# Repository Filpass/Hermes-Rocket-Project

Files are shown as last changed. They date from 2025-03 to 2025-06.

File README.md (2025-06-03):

# Hermes Rocket Project 🚀

This repository contains all software, data, and design files used in the development and flight testing of the Hermes Rocket.

## 📂 Contents

- `Design_Fabrication_and_Testing_of_a_3D_Printed_Model_Rocket_with_Integrated_Telemetry_Systems.pdf` – Master's thesis submitted for the M.Sc. in Space Engineering at Universität Bremen
- `/cad` – 3D models of nose cone, body tube, and adapter (.STL)
- `/code` – Python scripts for telemetry collection, live plotting, and post-flight analysis
- `/data` – Raw telemetry data from each flight (CSV format)
- `/analysis` – Static plots generated from telemetry

📄 [Download the full thesis (PDF)](./Design_Fabrication_and_Testing_of_a_3D_Printed_Model_Rocket_with_Integrated_Telemetry_Systems.pdf)

## 🛰️ Hardware Overview

- **Main Computer:** Raspberry Pi Zero 2W  
- **Sensors:**
  - GPS Module: PA1010D  
  - Barometric Pressure Sensor: DPS310  
  - 9-DOF IMU: ICM-20948 

## 📈 Output

Post-flight data visualization is located in the `/analysis` folder.

## 📹 Videos

Due to GitHub storage limits, flight camera and telemetry videos are hosted externally:  
🎥 [Watch on YouTube (Unlisted)](https://www.youtube.com/playlist?list=PLU9vdCkJsIVlVfhIgIDVsfnCWYGNboWbm)

## 📜 License

This project is open-source under the [MIT License](./LICENSE).

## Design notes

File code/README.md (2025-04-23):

# Hermes Rocket Project 🚀

This file contains all the python files that were used the project, in order to create this files the help of ChatGPT was used.

## Contents

- `camery.py` - Is the script for the camera to start recording
- `post_flight_plot.py` - Is the script in order to re watch the telemetry after the flight
- `receive_live2.py` - Is the script for the ground station in this case the macbook I had 
- `send_data3.py` - Is the script for the raspberry pi, specifically for the sensors to work. It needs to be run separately from the camera.py script as most of the libraries can only be used in a virtual environment
- `video_merge.py` - Is the script that merges all the video files and then converts them from .h264 to mp4 
- `flight_simulation.py` - Is the script that simulates the movement of the rocket based on its accelerometer and gyroscope data.

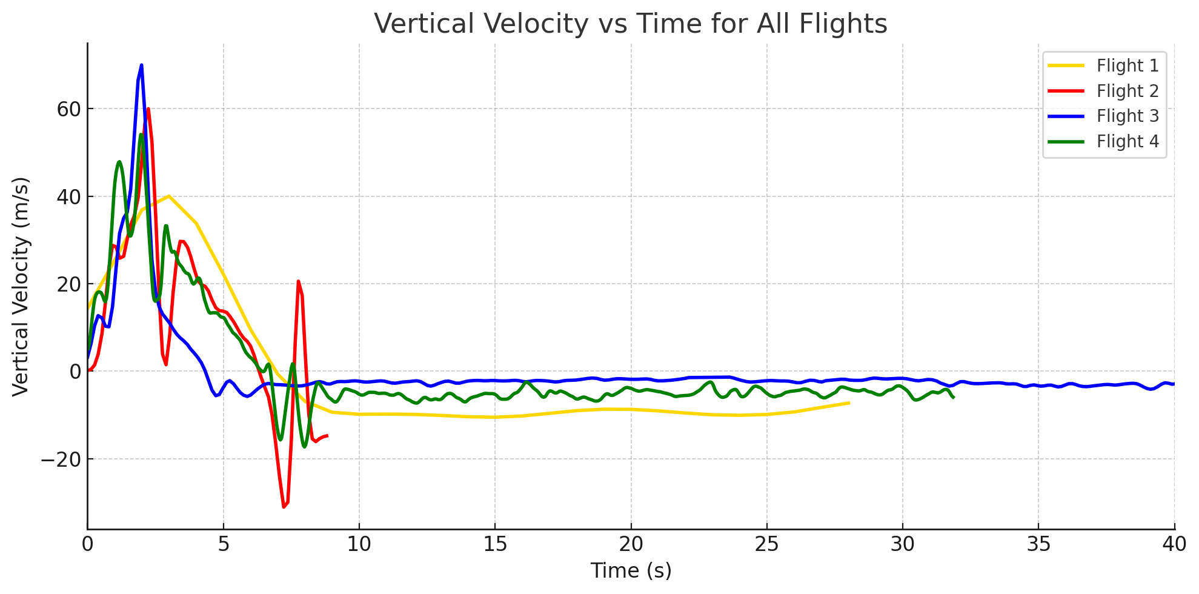
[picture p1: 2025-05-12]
analysis/Vertical Velocity vs Time for All Flights.png

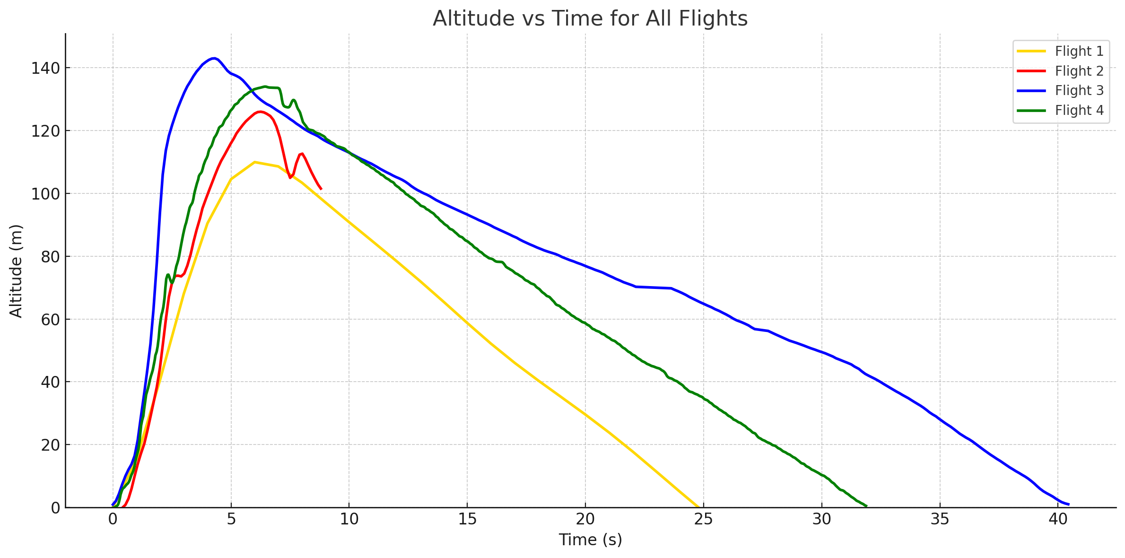
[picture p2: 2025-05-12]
analysis/Altitude vs Time for All Flights.png

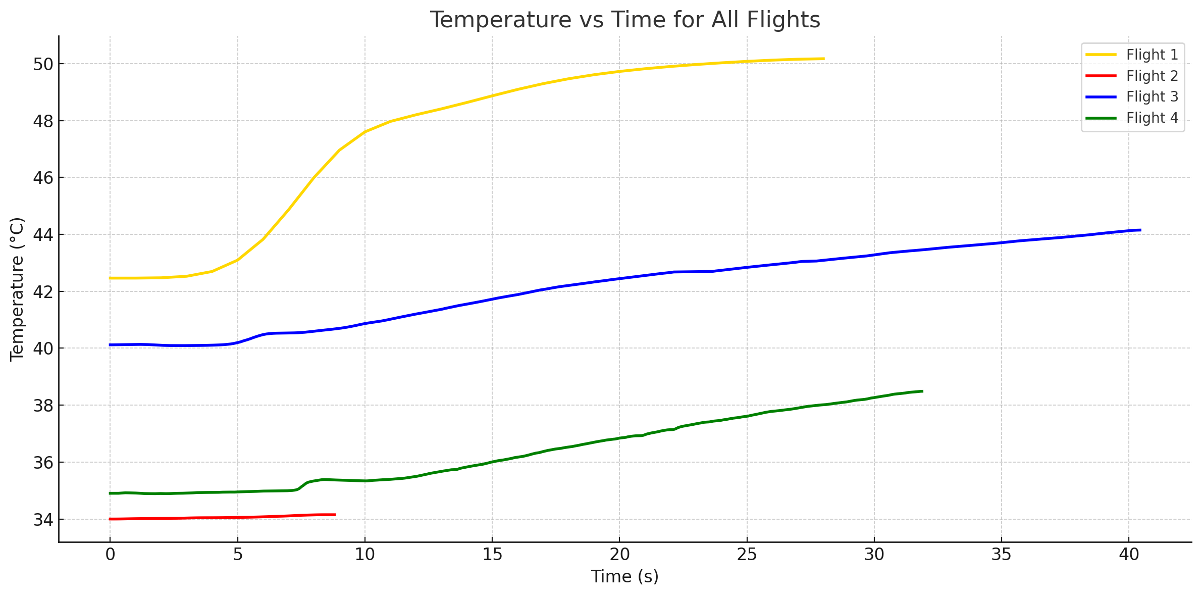
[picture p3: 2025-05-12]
analysis/Temperature vs Time for All Flights.png

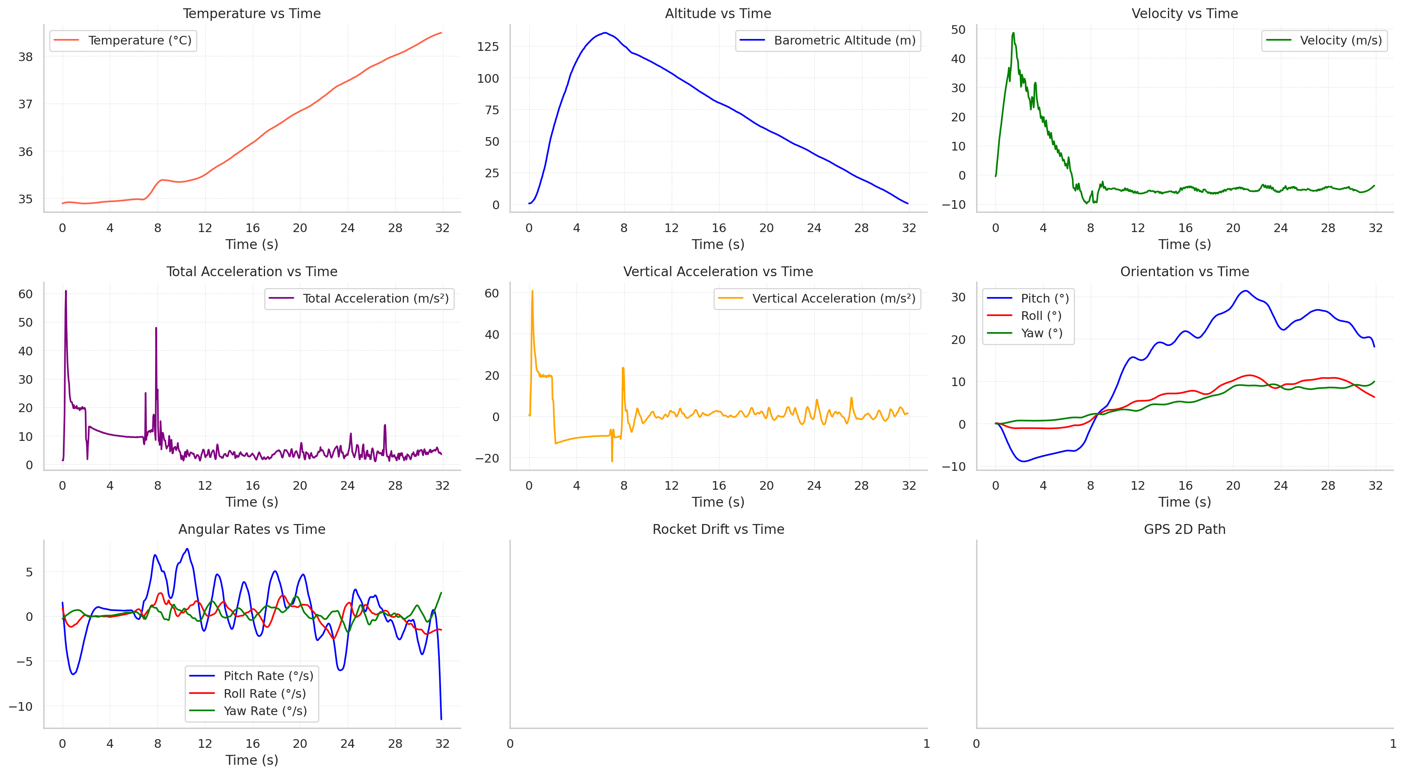
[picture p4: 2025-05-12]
analysis/Flight 4 - Telemetry.png

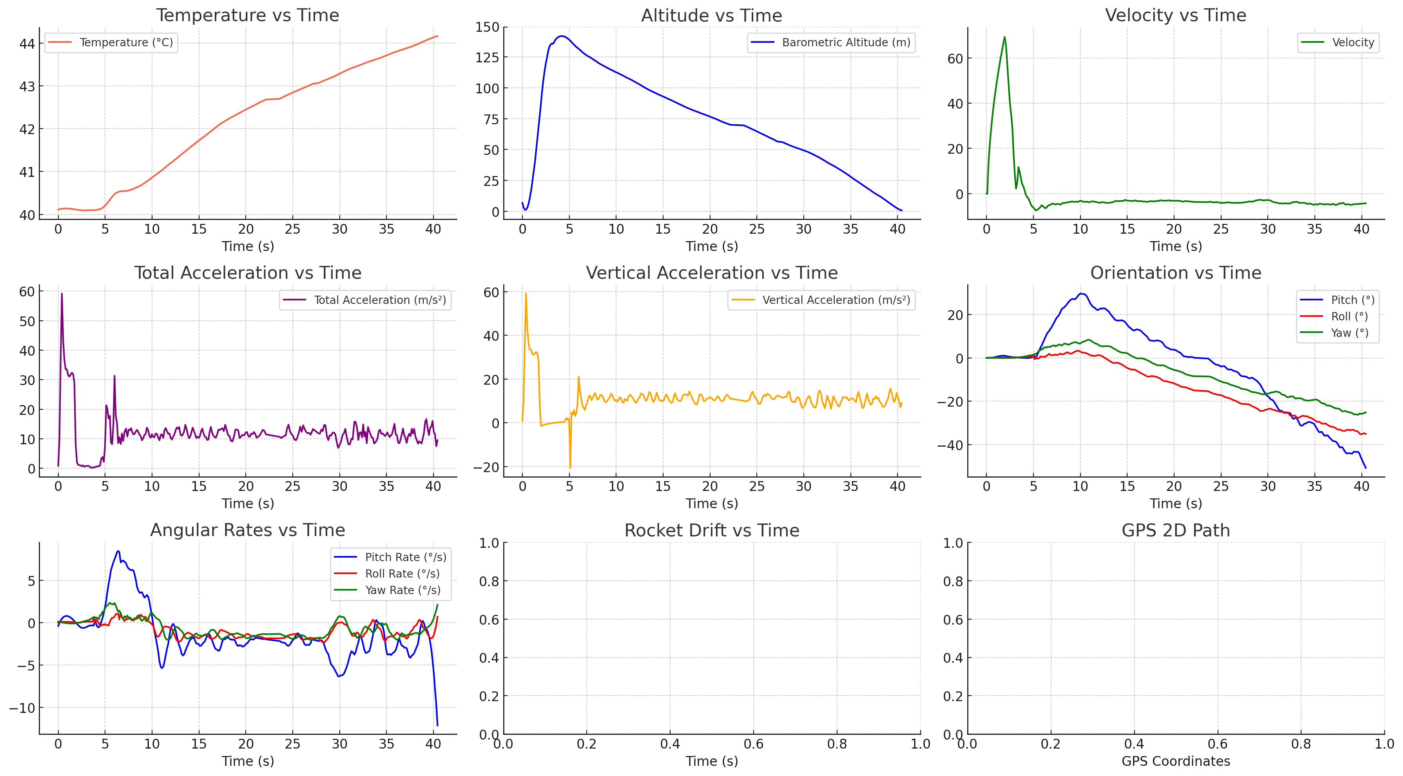
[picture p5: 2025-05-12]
analysis/Flight 3 - Telemetry.jpeg

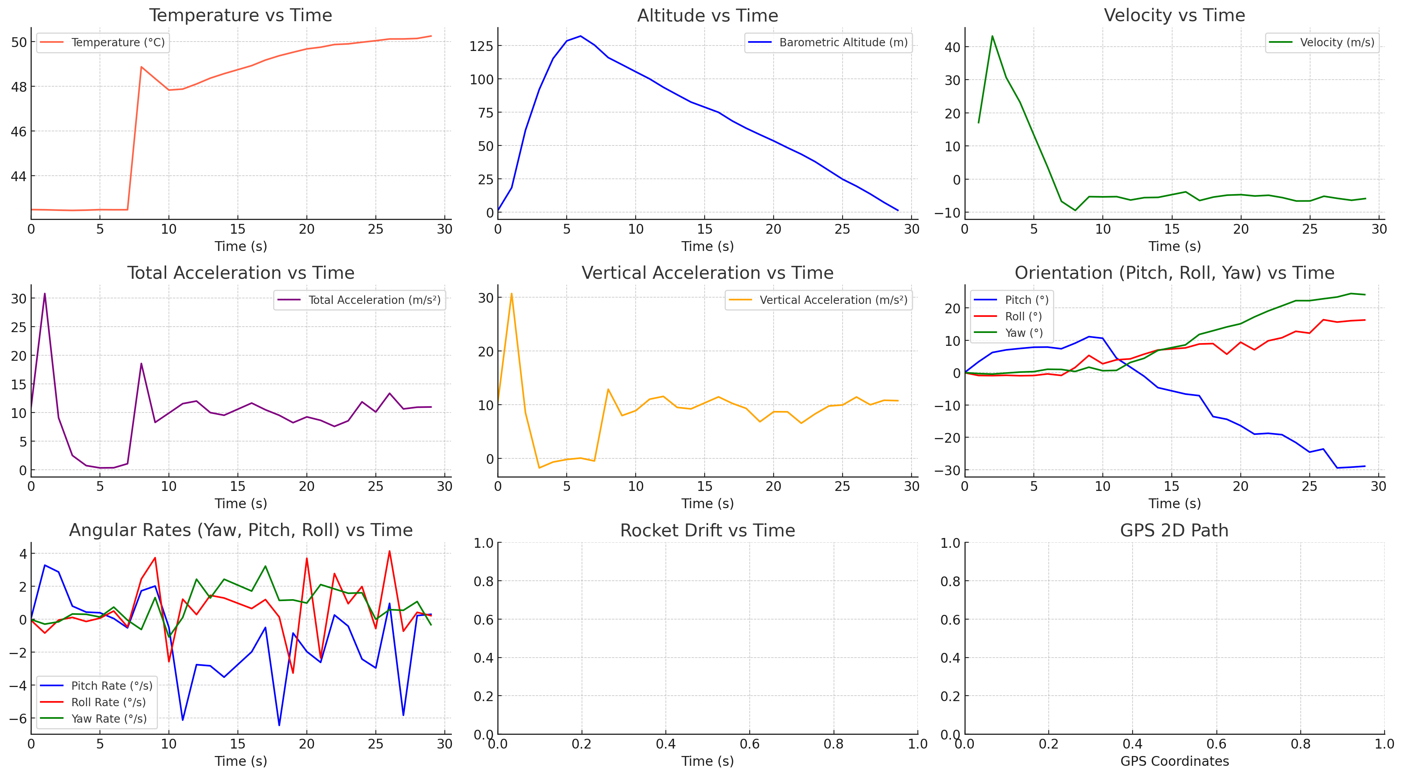
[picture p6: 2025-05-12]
analysis/Fligth 1 - Telemetry.png

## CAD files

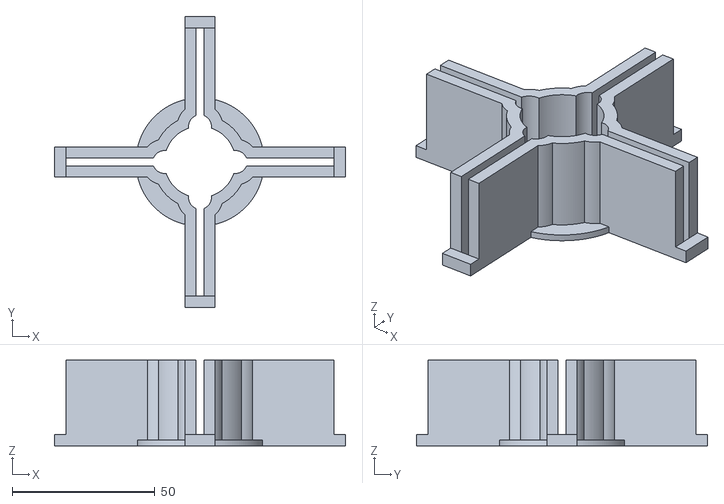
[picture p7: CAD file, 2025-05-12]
cad/Hermes Fin Aligner.stl
102.0 x 102.0 x 30.0

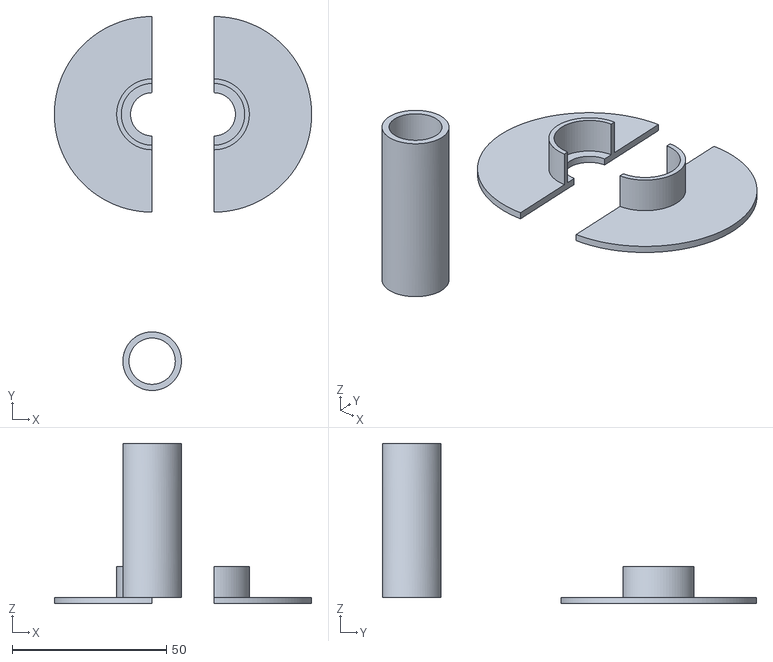
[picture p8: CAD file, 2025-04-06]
cad/Hermes Engine Protection.stl
83.4 x 121.2 x 52.0

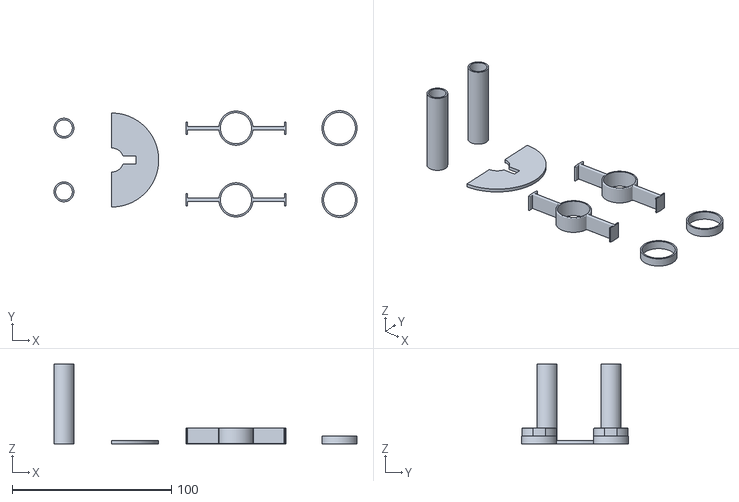
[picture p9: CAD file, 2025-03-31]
cad/Hermes Tubes.stl
190.2 x 67.0 x 50.0

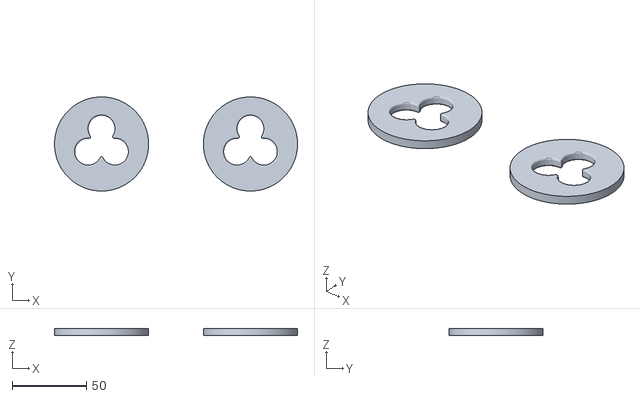
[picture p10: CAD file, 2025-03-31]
cad/Hemres BT Engine Mount.stl
163.2 x 63.2 x 5.00

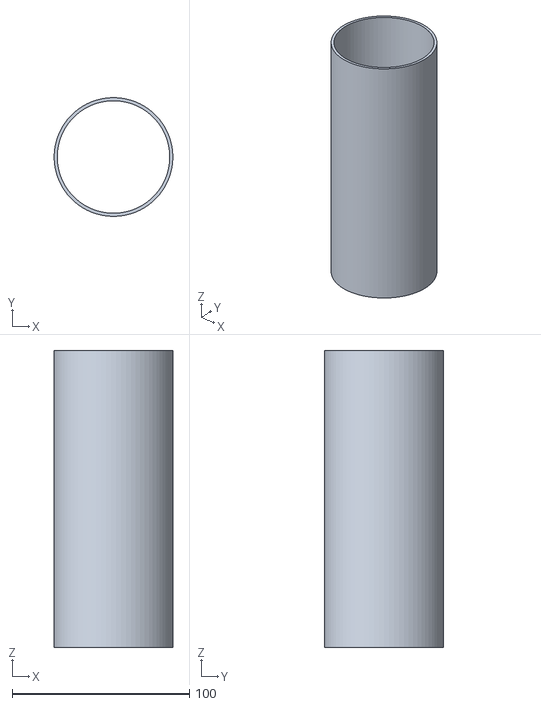
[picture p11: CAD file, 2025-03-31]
cad/Hermes BT.stl
67.0 x 66.9 x 167.5

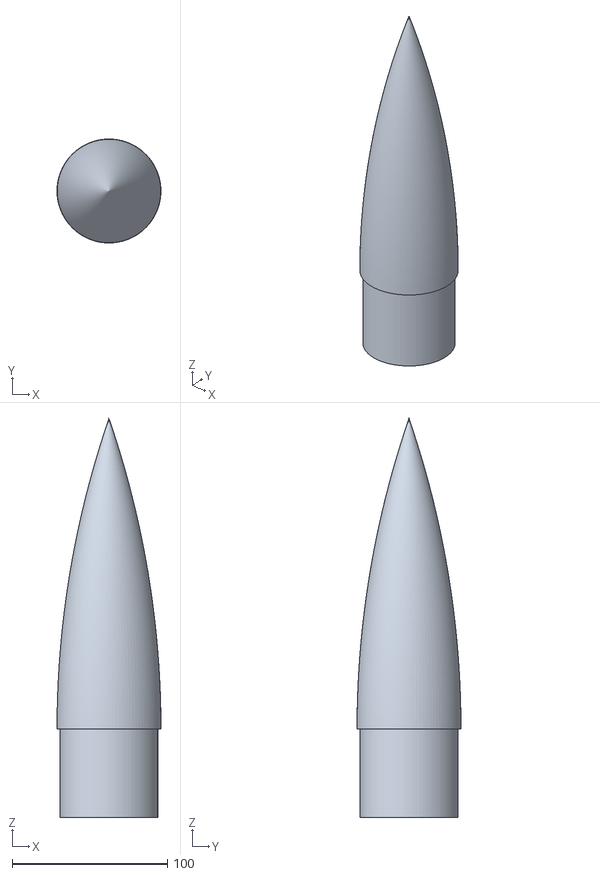
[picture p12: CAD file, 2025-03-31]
cad/Hermes NC.obj
67.0 x 67.0 x 257.0

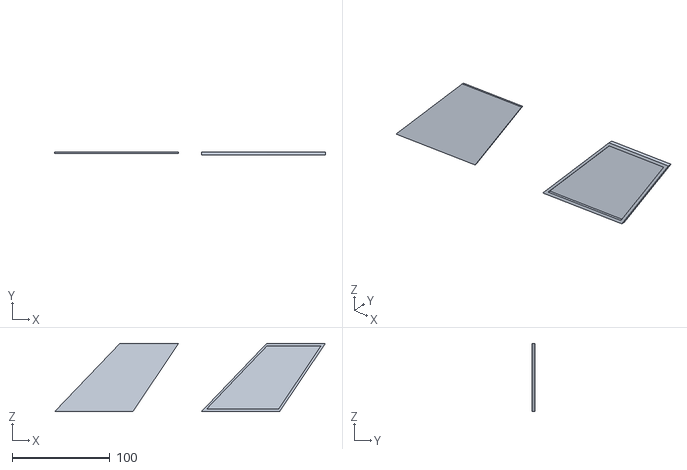
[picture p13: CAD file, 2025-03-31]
cad/Hermes Fin.stl
277.0 x 3.50 x 70.0

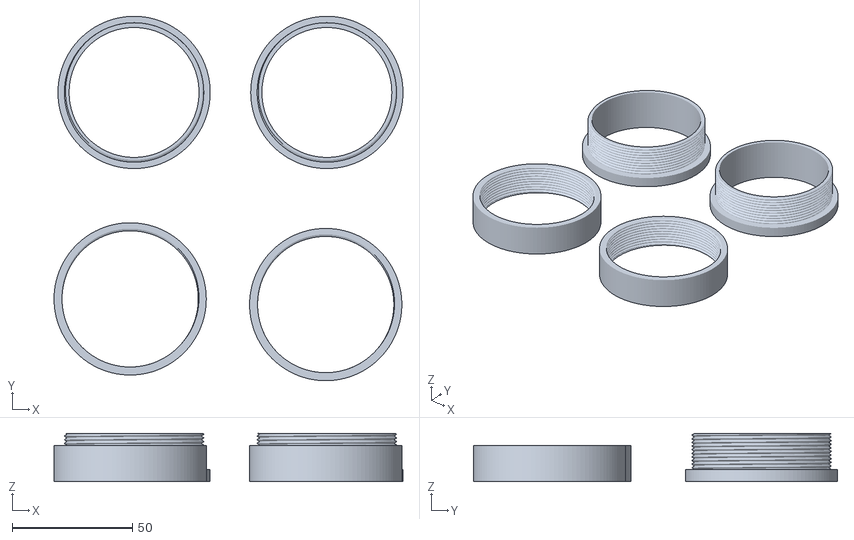
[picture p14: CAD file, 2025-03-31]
cad/Hermes BT Screwed Adapter.stl
144.8 x 151.2 x 20.0

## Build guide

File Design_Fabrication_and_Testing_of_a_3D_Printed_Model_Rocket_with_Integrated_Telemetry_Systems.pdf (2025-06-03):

## University of Bremen

## Faculty 4 Production Engineering

## Master Space Engineering I

## Master Thesis

# Design, Fabrication, and Testing of a 3D-Printed Model Rocket with Integrated Telemetry Systems

Author: | Philippos Georgios Moschidis Mat. Nr. 6254474
Date: | 06.06.2025
1. Reviewer: Dr.-Ing. Benny Rievers
2. Reviewer: Dr.-Ing. Florian Meyer

Supervisor: Dr. Petros Bithas

Philippos Georgios Moschidis Master Thesis
moschidis.filip@gmail.com
Matriculation Nr. 6254474

Design, Fabrication, and Testing of a 3D-Printed Model Rocket with Integrated Telemetry Systems

Entwurf, Herstellung und Test einer 3D-gedruckten Modellrakete mit integrierten Telemetriesystemen

Reviewers: Prof. Dr.-Ing. Benny Rievers & Dr. Florian Meyer Supervisors: Dr. Petros Bithas
University of Bremen
Space Engineering I (SpE I)
Faculty 4 Production Engineering ZARM, Am Fallturm 2
28359 Bremen

ii

## Abstract

The Hermes Rocket Project focuses on the integration of modern technologies into model rocketry through the design and fabrication of a 3D-printed rocket that includes a telemetry system. The objective of this study is to develop a costeffective and reusable model rocket capable of achieving an apogee of over 150 meters. The rocket is designed to collect flight data while it also utilises a camera to analyse the flight trajectory post-flight. The rocket has been designed to be lightweight and stable, while also ensuring structural integrity, based on PETG material and modular 3D-printed components. The flight computer, which has been custom-built, includes a Raspberry Pi Zero 2W microcontroller at its core, as well as three sensors: a GPS, an inertial measurement unit (IMU), and a barometric sensor to monitor altitude, pressure, and motion data. With these sensors we can monitor data which can be observed live during the start of the launch and more important they will be analysed post launch together with the onboard video footage. The propulsion of the rocket is provided by Klima D9-5 rocket engines, while the design, simulation and stability of the rocket were ensured through the use of OpenRocket software. The recovery system consists of a ripstop nylon parachute. There were four test flights completed that validated the rocket’s performance, telemetry accuracy, and recovery system. The flight data that were collected showed an okay alignment with OpenRocket simulations, with some deviations primarily because of environmental conditions and possibly motor performance. The results confirm the feasibility of using low-cost 3D-printed systems and off-the-shelf components for educational and experimental aerospace applications. This research shows how 3D printing and modern sensors can make model rockets easier to use and perform better, providing valuable information for educational and amateur aerospace projects.

iii

## Contents

1. Introduction | 2
2. Literature Review | 5
2.3. Role of Flight Computers and Telemetry in Model Rockets . . . . | 10
3. Rocket Design and Fabrication | 11
3.2.1. PLA, PETG, ABS, and Carbon Fiber Nylon Properties . . | 12
4. Flight Computer and Sensor Integration | 22
4.4.2. Data Logging, Visualization, and Ground Station Integration 30

iv

5. Propulsion System | 33
6. Rocket Simulation and Stability Analysis | 35
6.1.1. Centre of Gravity (CG) and Centre of Pressure (CP) . . . | 35
6.3. OpenRocket Documentation and Justification of Simulation
6.3.4. OpenRocket Simulation Features and Output Parameters . | 41
7. Recovery System Design | 43
8. Testing and Validation | 45
9. Results and Discussion | 48
10.Conclusion and Future Work | 72

v

10.4. Potential Applications of the Hermes Rocket | | 74
References | i
A. Project Repository | iii
B. Component List and Costs | iii
C. Launch Day Checklist | iii
D. Declaration of Consent | iv

vi

## List of Figures

1. Shady Side Academy Rocketry Club, Pittsburgh PA in January
| 1965. Rocketry enthusiasts from over a half century ago [2]. . . . | 2
2. | Hermes Rocket before the first Flight | | 3
3. | Four Forces in Flight [3] | | 5
4. Relativity Space’s third generation 3D-printer in its new head-
| quarters, with CEO Tim Ellis standing by for scale [9] | | 9
5. | Hermes Rocket with labeled parts | | 11
6. PLA, PETG, and ABS are the most common materials used with
| filament 3D Printers [12] | | 13
7. | Body Tube of Hermes on Fusion 360 | | 15
8. | Nose cone and Shoulder of Hermes on Fusion 360 | | 16
9. | Fins of Hermes on Fusion 360 | | 18
10. Hollow Interior Fin Design | | 18
11. The Original Prusa MINI+ Printer | | 19
12. The screwed adapter on Fusion360 and printed | | 20
13. The threaded adapter on Fusion360 | | 21
14. Flight Computer | | 22
15. Raspberry Pi Zero 2W and SparkFun Qwiic/STEMMA QT HAT
| [14] | | 23
16. Adafruit TDK InvenSense ICM-20948 [14] | | 25
17. Adafruit Mini GPS PA1010D [14] | | 25
18. Raspberry Pi Camera Module 3 - 12MP 120 Degree Wide Angle
| Lens [14] | | 26
19. LP903450 3.7 V 800 mAh Lithium Polymer Battery | | 27
20. The tube with the Raspberry Pi and sensors | | 28
21. Camera and GPS | | 29
22. Data Visualisation | | 32
23. Klima D9-5 engines | | 33
24. Thrust Curve of Klima D9-5 Engine [15] | | 34
25. Engine Mount on Fusion 360 | | 34
26. The three stability conditions with their CG-CP | | 36
27. Weight Distribution | | 37
28. A diagram of the rocket component classes [5] | | 38
29. The parachute system with dimensions | | 44
30. On-Board photo from Flight 1 | | 49
31. Telemetry data from the first flight | | 50
32. Flight 1 - Comparison of Actual and Simulated Altitude | | 51
33. Flight 1 - Comparison of Actual and Simulated Velocity | | 51
34. Flight 1 - Comparison of Actual and Simulated Total and Vertical
| Accelerations | | 52
35. Ejection Charge Protection System | | 53

vii

36. Telemetry data from the second flight | | 54
37. Flight 2 - Comparison of Actual and Simulated Altitude | | 55
38. Flight 2 - Comparison of Actual and Simulated Velocity | | 56
39. Flight 2 - Comparison of Actual and Simulated Total Acceleration | 56
40. Flight 2 - Comparison of Actual and Simulated Vertical Acceleration 57
41. Telemetry data from the third flight | | 58
42. On-Board photo from Flight 3 | | 59
43. Flight 3 - Comparison of Actual and Simulated Altitude | | 60
44. Flight 3 - Comparison of Actual and Simulated Velocity | | 60
45. Flight 3 - Comparison of Actual and Simulated Total Acceleration | 61
46. Flight 3 - Comparison of Actual and Simulated Vertical Acceleration 61
47. On-Board photo from Flight 4 | | 62
48. Telemetry data from the fourth flight | | 63
49. Flight 4 - Comparison of Actual and Simulated Altitude | | 64
50. Flight 4 - Comparison of Actual and Simulated Velocity | | 64
51. Flight 4 - Comparison of Actual and Simulated Total Acceleration | 65
52. Flight 4 - Comparison of Actual and Simulated Vertical Acceleration 65
53. Temperature Comparison of All Flights | | 66
54. Altitude Comparison of All Flights | | 66
55. Vertical Velocity Comparison of All Flights | | 67
56. Actual vs Simulated Flight Durations | | 68
57. Total Acceleration Comparison of All Flights | | 68
58. Controllable Surfaces on Fins by BPS.space [19] | | 74

viii

## List of Tables

1. | Comparison of 3D Printing Materials | | 12
2. | Comparison of Barometric Pressure Sensors [14] | | 24
3. Summary of key simulation assumptions in OpenRocket and their
| potential impacts on accuracy | | 42
4. | Requirement Description and Verification Method | | 45
5. | Flight Conditions and Environment Summary | | 48

ix

## List of Abbreviations

ABS | Acrylonitrile Butadiene Styrene
BMP | Barometric Pressure Sensor
CAD | Computer-Aided Design
Cal | Caliber (distance between CG and CP in body diameters)
CD | Drag Coefficient
CG | Centre of Gravity
CP | Centre of Pressure
DC | Direct Current
DOF | Degrees of Freedom
DPS310 | Digital Pressure Sensor 310
FDM | Fused Deposition Modeling
FPS | Frames Per Second
GND | Ground (electrical)
GPIO | General-Purpose Input/Output
GPS | Global Positioning System
HAT | Hardware Attached on Top
Hz | Hertz (sampling rate)
I2C | Inter-Integrated Circuit
IC | Integrated Circuit
IMU | Inertial Measurement Unit
J-B Weld | Commercial Two-Part Epoxy Adhesive
LED | Light Emitting Diode
mAh | Milliamp Hours
M58x1.5 | ISO Metric Thread (58 mm diameter, 1.5 mm pitch)
NAR | National Association of Rocketry
NASA | National Aeronautics and Space Administration
PETG | Polyethylene Terephthalate Glycol
PLA | Polylactic Acid
RAM | Random Access Memory
SBC | Single-Board Computer
SPI | Serial Peripheral Interface
STEM | Science, Technology, Engineering and Mathematics
STEMMA QT Adafruit Quick Connect I2C System
UDP | User-Datagram Protocol
V Voltage
°C | Degrees Celsius
°/s | Degrees per second
µA | Microamperes
µT | Microtesla

x

## Acknowledgement

I would like to thank several people whose support and guidance were crucial to completing my thesis. My academic supervisors, Dr. Benny Rievers and Dr. Florian Meyer, provided continuous guidance and constructive feedback throughout this process, and their support was very valuable. Their expertise was crucial to the completion of this thesis.

Additionally, I am especially thankful to my external supervisor, Dr. Petros Bithas, who without hesitation offered to help me with another thesis and whose contribution led to the successful completion of this project.

In particular, I would like to thank Mr. Theodoros Papafotiou for his support, very helpful ideas and for giving me access to the laboratory facilities of ’VROOM’, which were essential for the development of this thesis.

Finally, I wish to thank my family and friends for their support, patience and motivation during this challenging journey.

“Engineering is at the heart of space exploration, turning bold ideas into tangible achievements solving problems that were once considered impossible.”
− Aerospace Engineer

## 1. Introduction

### 1.1. Background and Purpose of the Study

The field of model rocketry started in the United States in 1957, it resulted from a synthesis of model aviation, the ancient art of pyrotechnics and modern rocket technology. It spawned the development of a novel and innovative approach to the field of model rocketry. Rocketry has for a long time been a platform for scientific exploration, offering students and hobbyists the opportunity to gain hands-on experience in propulsion, physics, aerodynamics, and engineering. In the past, model rockets were constructed by using basic tools and techniques, which restricted their ability to gather and analyse real-time flight data. But as engineering, compact computing, sensor technologies and engine manufacturing developed, it created opportunities for the design of high performance lightweight rockets. Additionally, the integration of telemetry, advanced sensors and 3Dprinting enables greater control over stability, more precise data collection and improved recovery mechanisms. The objective of the Hermes Rocket Project is to combine these technological opportunities with practical applications, thereby demonstrating how modern innovations can extend the limits of model rocketry [1].

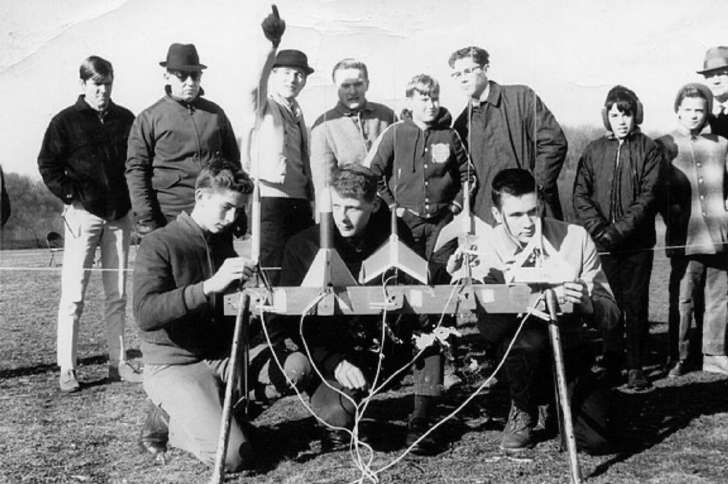
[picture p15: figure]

Figure 1: Shady Side Academy Rocketry Club, Pittsburgh PA in January 1965. Rocketry enthusiasts from over a half century ago [2].

### 1.2. Objectives of the Hermes Rocket Project

The scope of this thesis is to design, construct and launch a 3D-printed model rocket that is equipped with a custom-build flight computer that collects as well as transmits real-time telemetry data. The aim of this project is to explore the difficulties that come with integration of technologies including the Raspberry Pi, high-precision sensors, wireless communication, camera feed and wireless communication into the field of model rocketry. Additionally, a 3D printer will be used, in order for the Hermes Rocket Project to optimise weight, guarantee flight stability and finally make sure that the rocket is recovered safely for reusability. This study will provide helpful information and framework to the evolving field of model rocketry by integrating this modern technology with applications in education and amateur rocketry advancements.

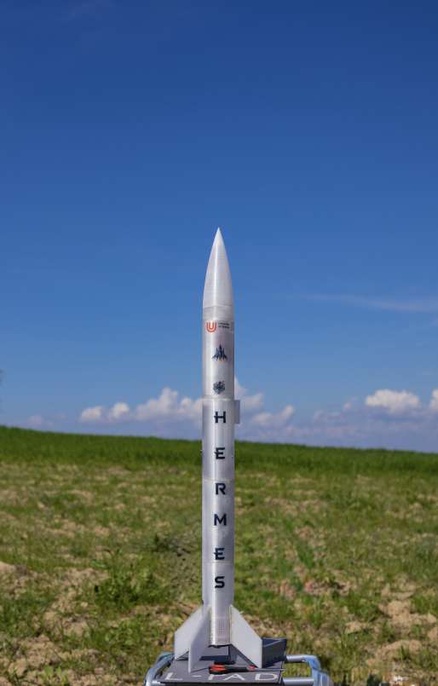
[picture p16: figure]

Figure 2: Hermes Rocket before the first Flight

### 1.3. Scope and Limitations

The main focus of this study is to design, manufacture and test the Hermes Rocket. After the 3D-print of the rocket, the assembly of the flight computer and the setup of the telemetry system were achieved, several tests were conducted with the objective of achieving a minimum apogee of 150 meters. In order for a safe recovery, a number of limitations were encountered during the course of the project. Some of these were the maximum print size of the 3D printer, the availability of the materials used for the rocket and the limited engine power as the project was self funded. Additionally as the testing was held under different conditions than the actual flight, some results may not be applicable to all scenarios. Finally, it should be noted that the project is an experimental design and not aimed for commercial production.

## 2. Literature Review

### 2.1. Overview of Model Rocketry

Model rocketry began in the mid-20th century as an educational and entertaining activity. It involves building scaled-down, functional versions of real rockets, often from lightweight, non-metallic materials, for instance paper, plastic or cardboard. This makes them affordable and safe, while factory-made solid-propellant motors guarantee reliability. A recovery system, such as a parachute, enables the rockets to return safely to the ground for reuse. Before 1958, model rocketry faced safety concerns, resulting in restrictions in many regions. However, the establishment of organisations such as the National Association of Rocketry (NAR) introduced standardised safety codes, making model rocketry a safe and popular hobby. Today, it is widely used as an educational tool to promote science, technology, engineering, and mathematics (STEM) concepts in schools, universities, and space camps [1].

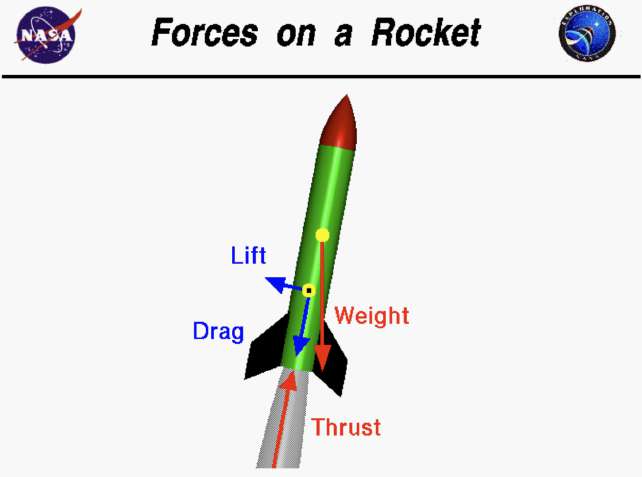
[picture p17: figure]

Figure 3: Four Forces in Flight [3]

Similar to aircraft, model rockets experience four primary forces during flight: weight, thrust, lift, and drag as they can also be seen in Fig. 3.

- Weight is the gravitational force acting on the rocket’s total mass, pulling it towards the Earth.
- Thrust acts as an opposing force to weight, enabling the rocket to overcome gravity and achieve lift-off.

- Lift stabilises and controls the rocket’s flight direction.
- Drag is the air resistance that slows down motion through the atmosphere.

One of the key features of stable flight is the relationship between the centre of gravity (CG) and the centre of pressure (CP). In order for a rocket to remain stable, the CP (which is determined by aerodynamic forces) must be positioned below the CG. This makes sure that, if there is wind or other disturbances, the rocket naturally returns to its intended flight path [3]. Additionally, the motion of a rocket can be described mathematically using the classical equations of motion, which are based on Newton’s second law. These formulations are described in detail in Rocket Propulsion Elements by Sutton and Biblarz [4],which will provide the basis for the following equations. The net force acting on the rocket is the combination of thrust, aerodynamic drag and gravitational force, as expressed in Eq. (1):

Fnet = m · a

Fthrust − Fdrag − Fgravity = m ·

d

2x
dt²

(1)

Continuing, Fnet is analysed in more detail below. The thrust Fthrust is produced by the expulsion of high-speed propellant mass, as followed in Eq. (2):

Fthrust = ˙m · ve | (2)
- Where:

– m˙ is the mass flow rate of the expelled propellant.

– ve is the exhaust velocity.

Additionally, the aerodynamic drag, the opposition of the rocket’s motion is an important factor that is calculated, as shown in Eq. (3):

Fdrag =

1
2
- Cd · ρ · A · v

2
(3)
- Where:

– Cd is the drag coefficient.

– ρ is the air density.

– A is the cross-sectional area.

– v is the velocity relative to the surrounding air.

Finally, the gravitational force is calculated as shown in Eq. (4):

Fgravity = m · g | (4)

These key equations, which are referenced in Eqs. (1) to (4), are important in order to understand rocket dynamics which are widely used in flight simulation tools [1], [5], [6]. The theoretical basis for rocket propulsion is based not only on Newton’s Second Law, but also on a number of important principles that are used to describe rocket performance. Sutton and Biblarz [4] provide an important insight into understanding both small-scale as well as full-scale rocket systems. One of the most important equations is the classical rocket equation that is also known as the Tsiolkovsky rocket equation. Which is describing how a vehicle produces acceleration by ejecting part of its mass at high velocity, following the principle of conservation of momentum. This equation, shown in Eq. (5), is critical for estimating the maximum velocity achievable by a rocket:

∆v = ve · ln

m0
mf

!
(5)
- Where:

– ve is the exhaust velocity.

– m0 is the initial mass.

– mf is the final mass after propellant has been burned.

Another significant performance metric is the specific impulse Isp, which measures how efficiently a rocket uses propellant fuel to generate thrust. It is expressed as thrust per unit weight flow of propellant and is given by Eq. (6):

Isp =

F
m˙ · g0

(6)

- Where:

– F is the thrust.

– m˙ is the propellant mass flow rate.

– g0 is the standard gravitational acceleration.

The overall thrust produced by a rocket engine is the result of momentum thrust and pressure thrust combined. The calculation is derived from the thrust equation, as illustrated in Eq. (7):

F = ˙m · ve + (pe − pa) · Ae | (7)
- Where:

– pe is the exit pressure.

– pa is the ambient pressure.

– Ae is the nozzle exit area.

Furthermore, the characteristic velocity is a metric of rocket engine combustion performance that is not reliant upon nozzle performance as shown in Eq. (8). It is therefore utilised for the purpose of comparing different propellants and propulsion systems.

c

∗ =

pc · At
m˙

(8)

- Where:

– pc is the chamber pressure. – At
is the nozzle throat area.

Additionally, the thrust coefficient, as demonstrated in equation Eq. (9), demonstrates a relation between the actual thrust produced and the chamber pressure and nozzle area, thereby offering insight into the performance of the nozzle design.

CF =

F

pc · At

(9)

Concluding, the law of conservation of mechanical energy connects the kinetic and potential energy of a system, as shown Eq. (10). In aerospace engineering, this link is used to calculate altitude gain, based on the principle that there are no losses due to drag or other forces [7].

E = Ek + Ep | (10)
- Where:

– Ek =

1
2mv²
is the kinetic energy.

– Ep = mgh is the gravitational potential energy.

– m is the mass of the object.

– v is the velocity.

– g is gravitational acceleration.

– h is the altitude.

By cancelling m on both sides of Eq. (11) and solving for h, we obtain:

1
2

mv² = mgh

h =

v

2
2g

(11)

This equation can be used in order to estimate the maximum altitude that can be achieved from a known velocity, assuming vertical motion and no aerodynamic losses. Together, these equations form a complete mathematical model for describing and analysing rocket performance, and are often used in research and engineering.

### 2.2. Advances in 3D Printing for Aerospace Applications

The introduction of 3D printing technology has begun a new era in manufacturing, offering opportunities for innovation and efficiency that were previously unattainable across a number of industries. Specifically, the aerospace industry benefited from the precision, durability, reduced weight, rigid prototyping and customisation that 3D printing provides. Materials used in additive manufacturing include: Polylactic Acid (PLA), Polyethylene Terephthalate Glycol (PETG), Acrylonitrile Butadi- ene Styrene (ABS) and Carbon Fibre Nylon and composites such as carbon-fibre- infused filaments. These materials are known for their strength, light weight, and ability to produce complex shapes that cannot be achieved using traditional manufacturing methods. Aerospace companies that have adopted 3D printing technology include SpaceX, NASA and Relativity Space [8].

Figure 4: Relativity Space’s third generation 3D-printer in its new headquarters, with CEO Tim Ellis standing by for scale [9].

Additive manufacturing can be applied in many different industries, as seen in its use for building model rockets. In particular, costs are significantly reduced compared to traditional machining, making advanced designs accessible to hobbyists. This is achieved by using 3D printing to create lightweight structures where the wall thickness, internal infill and material density can be controlled.

### 2.3. Role of Flight Computers and Telemetry in Model Rockets

As previously mentioned, flight computers have become important parts in the field of modern model rocketry, offering their users the ability to gather real-time data, monitor telemetry, and utilise autonomous control mechanisms. To be more precise, data collection refers to the gathering of information regarding altitude, velocity, orientation, temperature and pressure. This data can be recorded in real time during the flight for subsequent analysis. With regard to the telemetry system, this enables the transmission of live data to a ground station, thereby facilitating insights into the conditions of the flight. This enables the formulation of solutions to any issues that may arise with the rocket, including its position. Furthermore, flight computers can automate parachute deployment, thereby ensuring the safe return of the rocket. This can be achieved through the use of time-based triggers. In bigger scale rockets, the flight computers that are used, are capable of helping with stability of the rocket through the processing of the inertial measurement unit (IMU) data and then by correcting manoeuvres. Although flight computers can have many advantages, they also could present challenges. In order to function, the flight computer requires a power source. The issue may therefore lie in the management of this power, since the maintenance of a stable supply is imperative for the preservation of data integrity and the prevention of system failure. Additionally, external factors like vibrations, extreme temperatures, and rapid pressure changes can impact the accuracy and reliability of the sensors [1].

With reference to modern rocketry, there has been a notable increase in the accessibility of microcontrollers and sensors to the general public. This development has resulted in a significant role for flight computers in the collection of real-time data, the utilisation of telemetry, and the implementation of recovery mechanisms. The core of the flight computer is the microcontroller, which is primarily responsible for processing the data obtained from various sensors. These sensors may include a barometric sensor for measuring altitude, an IMU for orientation, and a global positioning system (GPS) for tracking. To facilitate live telemetry, wireless communication is essential, and onboard power management is necessary to ensure stable operation during flight.

## 3. Rocket Design and Fabrication

### 3.1. Conceptual Design of the Hermes Rocket

In order to achieve the scope of the project the rocket includes a flight computer, a camera and sensors for real-time collection of data. The objective of the mission is to achieve an apogee of around 150 metres, which will enable the flight computer and camera to gather a substantial amount of real-time telemetry and onboard video data for subsequent post-flight analysis.

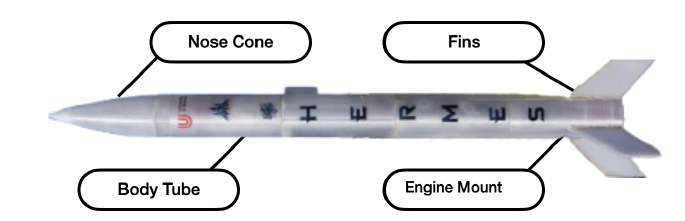
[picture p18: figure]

Figure 5: Hermes Rocket with labeled parts

The principal structural elements of the rocket are as follows:

- The body tube represents the primary structural component of the rocket. This constitutes the primary structural element of the rocket, wherein the flight computer, sensors, power supply and parachute for safe descent and durability will be positioned.
- The nose cone is also an important part of the rocket. It is positioned on the upper part of the rocket and is designed with an aerodynamic shape to minimise drag.
- The function of the fins is to maintain stability and control during flight. Their design is based on principles of weight distribution and aerodynamics.
- The engine mount is a device which is used to attach the rocket engine to the rocket structure. This is the location where the Klima D9-5 engines are situated, providing the thrust required for the rocket’s ascent.

The design philosophy is based on the principles of lightweight modularity. This approach allows for the construction of a rocket that is both lightweight and easily repairable. In case there would be a failure during any of the flights, the rocket could be re manufactured using the 3D printer, as the material is already bought and there is no need for additional design of the parts. The basic design of the rocket, as well as the flight simulations and stability analysis, were created using OpenRocket which is a free, open-source simulation software used for designing and analyzing model rockets. For the design of the rocket parts, the CAD application Autodesk Fusion 360 was used for 3D modelling.

### 3.2. Material Selection

Selecting the correct material for the manufacturing of the rocket is of great importance as it will impact its design and performance. In more detail the material will have an affect on the structural integrity, the aerodynamic efficiency, the thermal resistance as well as the overall weight. Factors that are essential for achieving a stable flight. In this section, a comparative analysis of the most commonly used 3D printing materials, namely PLA, PETG, ABS and Carbon Fibre Nylon is made, with respect to their strength, weaknesses, sustainability and price for the Hermes rocket. Every individual material has its distinctive advantages and disadvantages, thus it is important to select the optimal material that meets the most performance objectives for the rocket [8].

### 3.2.1. PLA, PETG, ABS, and Carbon Fiber Nylon Properties

The table below compares the properties of commonly used 3D printing materials.

Material | Strengths | Weaknesses
PLA | - Easy to print - Lightweight - Cost efficient | - Low heat resistance softens ∼ 60 °C. - Brittle
PETG | - Tough and flexible - Better heat resistance than PLA softens ∼ 80 °C - Slightly more expensive than the PLA | - Slightly harder to print than PLA - Slightly heavier than PLA
ABS | - Strong, durable and impact resistant - Better heat resistance than PLA softens ∼ 100 °C - Good machinability | - Dangerous fumes during printing - Tends to warp and crack
Carbon Fiber Nylon | - High heat resistance and vibration durability softens >100 °C - Flexible and excellent mechanical properties | - Expensive - More difficult to print

Table 1: Comparison of 3D Printing Materials

### 3.2.2. Trade-offs in Strength, Weight, and Durability

In order to select an appropriate material for the 3D printer, it is essential to consider the strengths and weaknesses of each material. It is of great importance that the rocket is sufficiently robust to withstand the launch and flight. But, it is also important to keep in mind that using materials that are excessively strong but also heavy may have a big impact on engine efficiency and apogee, as lighter materials improve performance. Additionally, when the engines ignite, they generate heat within the rocket, meaning the use of a material that is both heat-resistant and capable of maintaining its structural integrity under the influence of vibrations is very crucial.

As observed from Table 1, PLA is brittle and therefore unsuitable for applications involving high vibration or stress. In contrast, PETG, ABS and Carbon Fiber Nylon are characterised by high levels of toughness, with the latter exhibiting the greatest resilience. In terms of weight, PLA has the lowest mass, with PETG being a close competitor. ABS and Carbon Fiber Nylon have the highest mass. Ultimately, PLA and ABS have a high possibility of cracking, although the latter shows greater resilience to elevated temperatures. Furthermore, PETG has greater heat resistance than PLA, as well as better durability than the other materials. Finally, Carbon Fiber Nylon has a very good durability and can withstand high temperature [10] [11].

A comparison of the data in Table 1, together with the information on strength, weight and durability, concludes that Carbon Fiber Nylon is the optimal choice, with PETG being a good alternative. However, when considering cost, it is clear that Carbon Fiber Nylon is considerably more expensive than PETG. Consequently, the selected material for the Hermes rocket is be PETG.

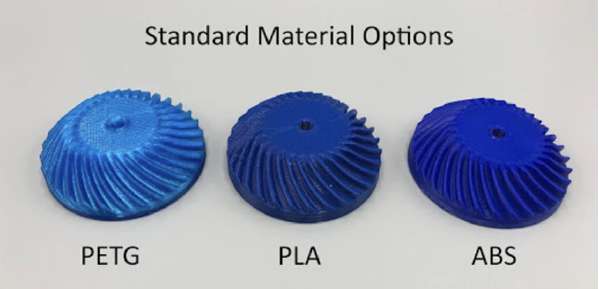
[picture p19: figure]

Figure 6: PLA, PETG, and ABS are the most common materials used with filament 3D Printers [12].

### 3.3. Hermes Rocket Design

This section addresses the design of the rocket and the weight of each component. A number of design guidelines and rules of thumb are employed in the field of rocketry. These rules will optimise performance, stability and aerodynamic efficiency. Prior to the design of the Hermes rocket, it is essential to consider a number of key factors in order to develop an effective and efficient design. It is imperative to consider the internal diameter of the body, as this will determine the location of the flight computer. The largest component of the flight computer has dimensions of 65 · 30 mm, which equates to a diameter of 67 mm.

### 3.3.1. Body Tube

With regard to the body tube, a rule of thumb for stability is that the length of the body tube should be approximately 9 to 10 times the maximum diameter of the rocket [1]. In Fig. 7 we can see that the outer diameter is 67 mm, the total length should be 670 mm and a suitable wall thickness for a robust and flexible body tube would be 1.8 mm. These dimensions allow us to calculate the weight of the body tube as shown in Eq. (12), Eq. (13), and Eq. (14). The material selected for this calculation is PETG, which has a density of 1.15 g
cm³

- The first step is to calculate the inner radius, using the difference between the outer radius and the wall thickness:

Inner Radius = Outer Radius − Wall Thickness
= 33.5 − 1.8 = 31.7 mm | (12)
- Next, the body tube volume is calculated using the cylindrical shell volume formula:

VBody Tube = π · hBody Tube ·

r

2
outer − r

2

inner

= π · 670 · (33.5

2 − 31.7

2
)
= 247020 mm³ = 247.02 cm³
(13)
- Finally, the weight is determined by multiplying the volume by the PETG density:

WeightBody Tube = Volume · Density

= 247.02 · 1.15 = 284.08 g | (14)

Therefore, the final mass of the body tube is determined to be 284.08 grams.

### 3.3.2. Nose Cone

The shape of the nose cone has an impact on the drag. The most common shapes observed in practice include conical, ogive and parabolic. Ogive and parabolic are typically more aerodynamically efficient than a simple conical shape. Furthermore, the ogive shape is more readily printable than the parabolic, which is

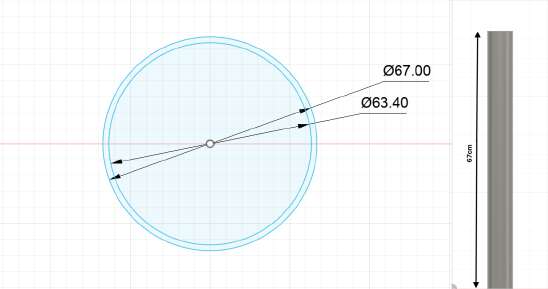
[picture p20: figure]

Figure 7: Body Tube of Hermes on Fusion 360

why this shape is typically selected. With regard to length, a widely accepted guideline is to maintain a ratio of between three and five times the diameter of the base to the length of the nose cone. This will ensure that the nose cone effectively reduces drag while also maintaining stability. Given that the diameter of the rocket is 67 mm, the length of the nose cone will be 200 mm. To calculate the weight, the following steps are undertaken, as shown in Eq. (15), Eq. (16), and Eq. (17) [6].

- The first step is to calculate the inner radius:

Inner Radius = Outer Radius − Wall Thickness
= 33.5 − 1.8 = 31.7 mm | (15)
- Next, the volume is calculated using the formula for a hollow cone:

VNose Cone =

1
3
- π · hNose Cone ·
r

2
outer − r

2

inner

=

1
3
- π · 200 · (33.5

2 − 31.7

2
)

=

1
3
- π · 200 · 117.36

= 23570 mm³ = 24.57 cm³
(16)
- Finally, the weight is determined by multiplying the volume by the material density:

WeightNose Cone = Volume · Density
= 24.57 · 1.15 = 28.26 g | (17)

It is also important to consider the shoulder of the nose cone which can be seen in Fig. 8. It is essential that the shoulder is of sufficient length to ensure stability during flight and to maintain the secure attachment of the nose cone to the body tube until the parachute deployment. The length of the shoulder should be sufficient to ensure that, upon ejection of the engines, the parachute is effectively deployed. The length of the shoulder is typically 1 to 1.5 times the diameter of the body tube.

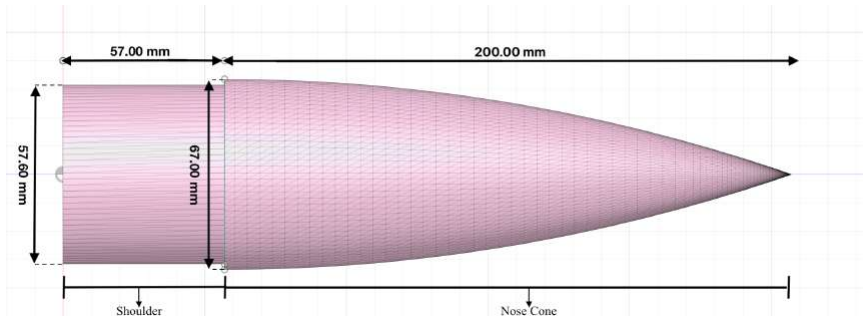
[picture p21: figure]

Figure 8: Nose cone and Shoulder of Hermes on Fusion 360

This would equate to a length of 57 mm for the shoulder. In this case, the wall thickness does not have to be the same as that of the body tube or the nose cone, but it can be thinner. In this instance, it will be 0.1 mm. To calculate the weight of the shoulder, the following steps are undertaken, as shown in Eq. (18), Eq. (19), and Eq. (20) [1].

- The first step is to calculate the inner radius:

Inner Radius = Outer Radius − Wall Thickness
= 33.5 − 1 = 32.5 mm | (18)
- Next, the volume is calculated:

VShoulder = π · hShoulder ·

r

2
outer − r

2

inner

= π · 57 · (33.5

2 − 32.5

2
)
= π · 57 · 66
= 118100 mm³ = 11.81 cm³
(19)
- Finally, the weight is calculated by multiplying the volume by the density:

WeightShoulder = Volume · Density
= 11.81 · 1.15 = 13.59 g | (20)

The final mass is obtained by adding the weight of the nose cone and the shoulder, resulting in a value of 28.26 + 13.59 = 41.85 grams. But the actual final volume was not the same as calculated, Fusion 360 showed that the volume is 60.18 cm³ and the mass is calculated in Eq. (21):

- Finally, the combined weight of the nose cone and shoulder is calculated:

WeightNC&Shoulder = Volume · Density
= 60.18 · 1.15 = 69.2 g | (21)

### 3.3.3. Fins

The fins on a model rocket are also very important because they are crucial for maintaining the rocket’s stability. They make sure that the rocket maintains a straight trajectory, stopping it from moving sideways. A rocket typically has three or four fins, for Hermes the selection of fins is four as they provide more stability than three fins would. The rules of thumb used for the fins are based on this source [1]. The fin height should be between 0.5 to 1.2 times the rocket diameter, given that the diameter of the Hermes model rocket is 67 mm, the height of the fins should be 70 mm. The root chord should be between one and one-and-a-half times the diameter of the rocket. In this case, the root chord will be 80 mm. The tip chord is typically between 50 and 80 percent of the root chord, which in this case will be 60 mm. With regard to the sweep length, this should be between 60 and 80 percent of the root chord, here it is 67 mm. The optimal sweep angle is between 30 and 45 percent of the root chord in this case it is 43.7 °. The fins will be 5 mm thick to make sure that they have enough strength while maintaining a low weight. These dimensions are illustrated in Fig. 9 below, and they allow us to calculate the weight of the fins, as shown in Eq. (22) and Eq. (23). The material selected for this calculation is PETG, which has a density of 1.15 g
cm³

. The fins were designed with a hollow interior in order to optimise weight. While a typical single-piece fin is more straightforward to manufacture, it would result in an excess of mass that could have a detrimental impact on the rocket’s stability margin and apogee. In order to address this issue, the two-part design consists of one edge wall layer which has a flat base and a wall attach and another flat base by itself, as it can be seen in Fig. 10. The hollow design results in a notable reduction in the mass of the fins without any compromise to their strength or aerodynamic properties.

- The weight of a single fin is calculated:

WeightFin = Volume · Density
= 16.2 · 1.15 = 18.6 g | (22)
- Since the rocket has four fins, the total weight is:

WeightFins = WeightFin · Number of Fins
= 18.6 · 4 = 74.5 g | (23)

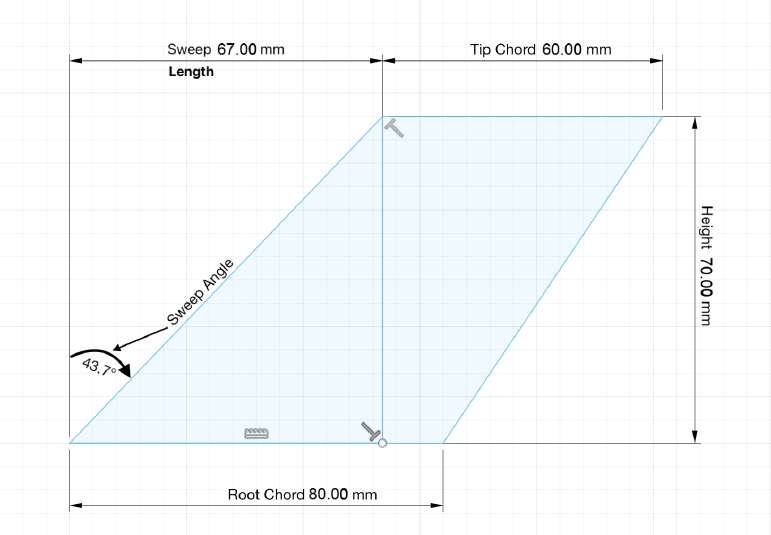
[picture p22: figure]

Figure 9: Fins of Hermes on Fusion 360

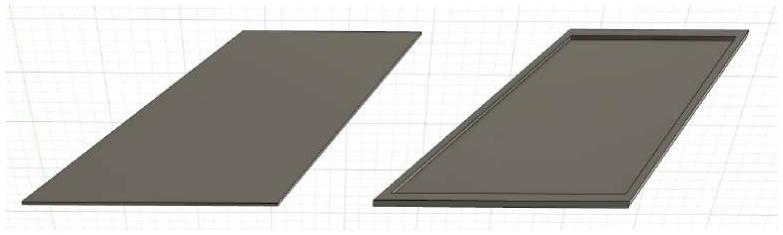
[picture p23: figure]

Figure 10: Hollow Interior Fin Design

In comparison, had a solid design been employed, the weight of a single fin would have been 28 grams, resulting in a saving of 10 grams per fin.

### 3.4. 3D Printing Process

### 3.4.1. Printer characteristics and Constraints

Regarding the 3D printer, the Prusa MINI+ shown in Fig. 11 was used. It is fitted with a sensorless homing mechanism, automated mesh bed calibration, interchangeable nozzles, network connectivity, USB printing and a full-colour LCD screen. The layer height of the printer ranges from 0.05 mm to 0.25 mm, with the nozzle set to 0.04 mm by default and the ability to accommodate filament diameters of up to 1.75 mm. The printer is compatible with a multitude of materials, including PETG, as previously stated. Additionally, the maximum permissible temperature for the nozzle is 280 °C, while the maximum permissible temperature for the bed is 100 °C. It is also notable that the print volume is 180 · 180 · 180 mm. However, to enable printing of more complex designs and better results, this has been modified to 170 · 170 · 170 mm [13].

Figure 11: The Original Prusa MINI+ Printer

### 3.4.2. Assembly of Body Tube, Nose Cone, and Shoulder

The assembly of the Hermes rocket is a process of aligning and connecting the main components in order to ensure structural integrity and aerodynamic efficiency. The four body tubes are stacked in a vertical configuration. The nose cone is affixed to the uppermost body tube via a precision-engineered shoulder joint. This design feature serves two purposes: firstly, to maintain stability during flight, and secondly, to facilitate the deployment of the recovery system. As the rocket is constructed from multiple components, they must be assembled. In the case of components that are to remain connected on a permanent basis, the use of a durable bonding agent such as epoxy glue is essential to ensure a robust and long-lasting attachment. However, in order to facilitate access to the internal components for maintenance or modifications, the modular assembly simplifies both the construction process and any future adjustments, thereby ensuring flexibility for testing and optimisation.

### 3.5. Joining Methods and Structural Testing

### 3.5.1. Epoxy Bonding

In order to achieve a good epoxy bond with the PETG material that was selected, it is important to use a glue that is specifically formulated for this purpose. The J-B Weld Plastic Bonder was selected as the optimal choice. The adhesive has a rapid setting time and is a two-part glue. The glue was employed for the fins, both for affixing the edge wall layer to the flat base layer and for attaching the entire fin to the body tube. Furthermore, the adhesive was employed for the nose, as previously stated, due to its two-part printing configuration.

### 3.5.2. Adapter-Based Screwed Connections

With regard to the adapter connections, the adapter is composed of two rings that are affixed to the interior of the tube. These rings are then glued at the base of one tube and the top of the other. The interior of the adapter features four holes through which the screw and threaded inserts were positioned. This configuration allows for the straightforward disassembly of the body tube, thereby facilitating access to the flight computer. The adapter is illustrated in greater detail in Fig. 12.

Figure 12: The screwed adapter on Fusion360 and printed

### 3.5.3. Adapter-Based Threaded Connections

Another concept for joining methods was fabricating a three-dimensional printed threaded adapter. To create this, two cylindrical components were designed, one male and one female, as shown in Fig. 13. The female component on the left has an internal diameter of 59.2 mm and the male component on the right has an internal diameter of 57.9 mm, providing a suitable clearance fit. Both components use an ISO metric thread profile with a triangular geometry and a flank angle of 60°, ensuring compliance with international standards. The thread size is M58x1.5, 57.9 mm is the nominal diameter and 1.5 mm is the thread pitch, ensuring a fine, precise fit. With regard to the female component, a 6H tolerance class was selected, representing a standard internal thread fit. In contrast, the male component employs a 6g class, ensuring a medium external tolerance. This combination ensures a reliable, slightly loose fit that accounts for potential inaccuracies inherent to the 3D printing process.

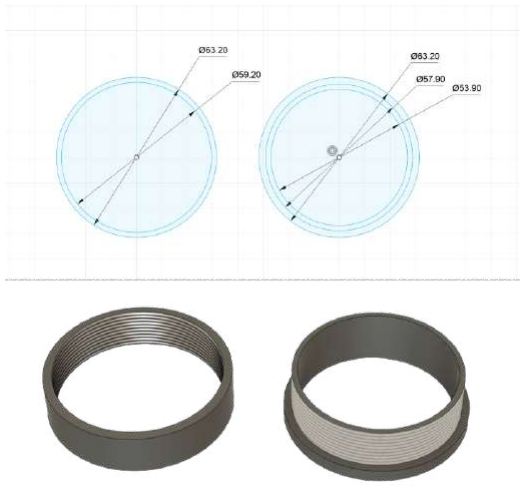
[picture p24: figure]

Figure 13: The threaded adapter on Fusion360

Following a comprehensive evaluation of the three proposed methods, namely epoxy glue, screwed-based adapter and threaded-based adapter, it was determined that the threaded adapter, due to its superior ease and convenience, was the optimal choice. The primary rationale for this determination was the ability to access all body tubes at any given moment, in contrast to the screwed connection. If modifications were to be made to the body tube in proximity to the engines, the necessity to unscrew every other component would be required.

## 4. Flight Computer and Sensor Integration

### 4.1. Overview of the Flight Computer System

The flight computer is the rocket’s central component, which is responsible for collecting and storing data during the flight. It is also considered as the payload of the Hermes Rocket. Its primary function is to monitor and log important flight information, such as altitude, pressure, temperature and motion data, while also transmitting live telemetry to the ground station for real-time analysis. Additionally, it is equipped with a camera to capture video footage. This system ensures accurate data collection for post-flight analysis and performance evaluation.

The core components of the flight is the microcontroller, which in this instance is the Raspberry Pi Zero 2W. Additionally, a Hardware Attached on Top (HAT) was placed to the Raspberry Pi, which is equipped with Qwiic output, this will facilitate a more straightforward connection with the sensors. Additionally, the sensors will be located in various positions across the rocket, thereby saving space and enabling the rocket to be narrower and with an improved weight distribution. The flight computer has a variety of sensors in order to achieve its goals, this includes motion sensors like the IMU, pressure and temperature sensors, a GPS module and a camera module which can be seen in Fig. 14. Details of the specifications, functions and capabilities of the sensors can be found in Section 4.2. Finally the flight computer is powered by a lightweight battery system to ensure stable operation while maintaining the overall weight limits of the Hermes rocket.

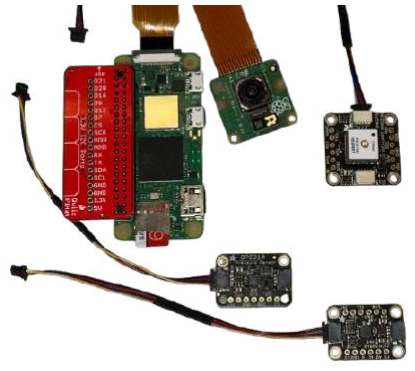
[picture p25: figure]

Figure 14: Flight Computer

### 4.2. Component Selection and Specifications

### 4.2.1. Microcontroller

The microcontroller that was selected is the Raspberry Pi Zero 2W as it has a compact size, it is low weight and has sufficient computational power to handle real-time data processing and transmission. Other options were the Arduino Nano, the Arduino Due, and the STM32F103C8T6 (also known as the Blue Pill). But, ultimately these options were unsuitable due to the Arduino Nano not being able to support additional sensors, the Arduino Due being to heavy, and finally the lack of compatibility with the required camera functionality of the Blue Pill. The Raspberry Pi, is equipped with a quad-core CPU and 512MB of RAM, which makes sure it is able to process multiple sensor inputs and handle real-time telemetry transmission. Finally, it has a low power consumption allowing it to operate efficiently on a 7.4W battery setup [14].

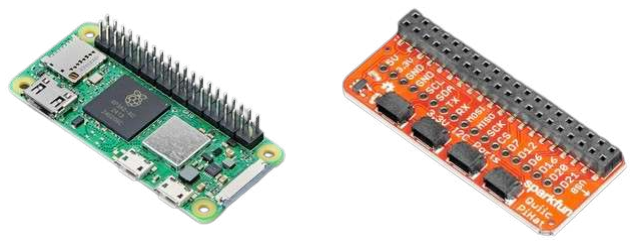
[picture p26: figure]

Figure 15: Raspberry Pi Zero 2W and SparkFun Qwiic/STEMMA QT HAT [14]

Furthermore, the Raspberry Pi offered the additional option of a HAT which can be seen in Fig. 15, it greatly simplified the connection with the sensors, eliminating the need for soldering. The selected HAT is the SparkFun Qwiic/STEMMA QT HAT for Raspberry Pi. The device facilitates the connection of the Inter-Integrated Circuit (I

2C) bus - including Ground (GND), 3.3 Volt (3.3V), Serial Data (SDA), and Serial Clock (SCL) - on the Pi to an array of Qwiic connectors on the HAT. The Pi HAT is equipped with four Qwiic connect ports, all on the same I

2C bus. Additionally, the device is compatible with any Pi or single-board computer (SBC) that features a standard 2x20 General-Purpose Input/Output (GPIO) header [14].

### 4.2.2. Sensor Selection

As for the selection of the pressure sensors, the BMP180, BMP280, BMP388, and the DPS310 were considered. The technical specifications can be seen in Table 2.

By comparing the DPS310 and the BMP388 it can be seen that they are more precise in their pressure measurements and have a considerably broader range than the other sensors. Continuing with the altitude measurements, the DPS310 is the most precise of the sensors, offering a resolution of 20 mm, which makes it the optimal choice in this context. Furthermore, for the BMP388 and the DPS310 the sampling rate is considerably superior to that of the other sensors, and they are also more efficient during active operation. Also, the DPS310 and BMP388 offer the highest accuracy of ±0.5 °C, making them the optimal choice for the recording of temperature. While the BMP388 is also a strong contender, the DPS310 offers precision, resolution, and low power consumption, making it the most suitable option for flight computers where accuracy and efficiency are very important [14].

Feature | BMP180 | BMP280 | BMP388 | DPS310
Pressure Range | 300-1100 hPa | 300-1100 hPa | 300-1250 hPa | 300-1200 hPa
Pressure Acccuracy | ±1.0 hPa | ±0.12 hPa | ±0.08 hPa | ±0.5 hPa
Altitude Resolution | ∼10 mm | ∼10 mm | ∼10 mm | ∼20 mm
Temperature Range | 0 to 65 °C | -40 to 85 °C | -40 to 85 °C | -40 to 85 °C
Temperature Accuracy | ±2.0 °C | ±1.0 °C | ±0.5 °C | ±0.5 °C
Sampling Rate | ∼3 samples/sec | 1 - 25 Hz | 1 - 200 Hz | 1 - 128 Hz
Power Consumption | ∼12 µA | ∼2.7 µA | ∼3.4 µA | ∼3 µA
Interface | 2C / SPI I | I 2C / SPI | I 2C / SPI | I 2C / SPI
Size (mm) | 3.6x3.8x0.93 | 2.0x2.5x0.95 | 2.0x2.0x0.75 | 2.0x2.5x1.0

Table 2: Comparison of Barometric Pressure Sensors [14]

The range of motion sensors available for selection was less extensive than that of pressure sensors. The principal options were the MPU6050 and the ICM-20948, which may be regarded as a moderately enhanced iteration of the MPU9250. The key differentiating factors between the two are as follows: the MPU6050 is a 6-axis IMU that provides data from accelerometers and gyroscopes, whereas the ICM-20948 is a 9-axis IMU that provides the same data and is also a magnetometer with a ±4900 µT range, enabling full 3D orientation tracking with enhanced precision. The ranges of the accelerometer (range : ±2 g, ±4 g, ±8 g, ±16 g) and the gyroscope (range : ±250 °/s, ±500 °/s, ±1000 °/s, ±2000 °/s) are identical. Moreover, the ICM-20948 exhibits markedly superior power efficiency, consuming only 1.23 mA in contrast to the 3.6 mA consumed by the MPU6050. The

ICM-20948 operates at a voltage range of 1.71 V to 3.6 V, whereas the MPU6050 necessitates a voltage range of 3.3 V to 5 V. Furthermore, both sensors have comparable sampling rates. Finally, the ICM-20948 has a smaller size and supports both I2C and SPI, and can be readily obtained with STEMMA QT/Qwiic connectors. Therefore, the ICM-20948 which can be seen in Fig. 16, with its 9-axis capability, magnetometer integration, and low power consumption, is more suitable for high-precision orientation tracking [14].

Figure 16: Adafruit TDK InvenSense ICM-20948 [14]

In regard to the GPS selection, given that the microcontroller in use is the Raspberry Pi with Qwiic connectors, the sole viable option is the Adafruit Mini GPS PA1010D as depicted in Fig. 17. The device is a compact and efficient GNSS module that supports the GPS satellite system and offers a position accuracy of ±3 metres and a timing accuracy of ±30 nanoseconds under open-sky conditions. It operates within a voltage range of 3.0 V to 4.2 V, with an active power consumption of approximately 20 mA. Furthermore, the device has also a built-in ceramic patch antenna, ensuring reliable operation in challenging environments. Moreover, the GPS is designed to withstand extreme conditions, as it can operate from −40°C to +85°C and has a maximum altitude of 18000 metres, making it very suitable for rocket flights with a high altitude. Finally, its compact dimensions (11 · 11 · 2.2 mm) and lightweight design make it an optimal selection for this project [14].

Figure 17: Adafruit Mini GPS PA1010D [14]

### 4.2.3. Raspberry Pi Camera

In regard to the camera selected for this project, the decision to utilise the Raspberry Pi Camera was an appropriate one, given that it is easily connected to the microcontroller, which has a designated port for this purpose. This choice was made in light of the fact that the microcontroller in use is the Raspberry Pi. Three options were available: the Raspberry Pi camera module 2, the camera module 3, and the camera module 3 with a wide-angle lens. The second generation has an 8-megapixel resolution, in comparison to the 12-megapixel resolution of both the Camera Module 3 options, which also support autofocus and high dynamic range. The field of view represents a further distinguishing feature between the models. The module 2 offers a horizontal field of view of 62.2 °, the standard module 3 a 66 ° field of view, and the wide lens a 120 ° field of view. The remaining features, including the CSI interface, weight, low power consumption, and dimensions, are largely consistent across the options. With regard to cost, the module 3 is available at a comparable price point. For this project, the camera module 3 with the wide lens as seen in Fig. 18 is the optimal choice due to its capacity to capture a broader perspective, which aligns well with the requirements of dynamic, high-altitude environments [14].

Figure 18: Raspberry Pi Camera Module 3 - 12MP 120 Degree Wide Angle Lens [14]

### 4.2.4. Power Supply

The power supply represents a crucial element of the flight computer system, ensuring the dependable functioning of all electronic components throughout the rocket’s flight. The system has been designed to meet the electrical requirements of the Raspberry Pi Zero 2W, sensors and camera module, while also maintaining a lightweight and compact design. The total power requirement of the flight computer system was calculated based on the following components: The Raspberry Pi Zero 2W has a typical consumption of 1.2 W at 5 V, the DPS310 and ICM-20948 sensors have a combined power consumption of less than 5 mA, the GPS module has around 20mA consumption during operation and the Camera Module 3 has an additional load of 200 mA during active recording. To calculate the power consumption, the following steps were undertaken, as shown in Eq. (24), Eq. (25), Eq. (26), and Eq. (27).

- The current for the Raspberry Pi Zero 2W is calculated:

Current (mA) =

Power (W)
Voltage (V)

=

1.2
5
= 250 mA | (24)
- Adding up the current consumption of all the components:

Total Current Draw = 240 (Pi) + 5 (Sensors) + 20 (GPS) + 200 (Camera)
= 465 mA | (25)
- Assuming the system operates continuously for 15 minutes (including flight computer testing before launch), the conversion into hours is:

Flight Duration (hours) =

15
60
= 0.25 hours | (26)
- The total energy consumed during this time is:

Energy Required (mAh) = Current Draw (mA) · Flight Duration (hours)
= 465 · 0.25 = 116.25 mAh | (27)

In order to satisfy the requirements mentioned above, it is necessary to use a battery that has a voltage more than 5V and a total capacity of 200 mAh, in order to accommodate safety margins. Consequently, the battery that was selected is the Cellevia Battery LP903450 as seen in Fig. 19, which is a 3.7 V, 800 mAh lithium polymer battery. The battery was also selected as its weight is equivalent to that of the Raspberry Pi, thus serving the function of a counterweight. Furthermore, a step-up converter was used in order to upgrade the voltage output.

Figure 19: LP903450 3.7 V 800 mAh Lithium Polymer Battery

### 4.3. Sensor integration on Rocket

The positioning of sensors is of paramount importance for ensuring the stability of a rocket, given that the weight distribution is not uniform and one side of the rocket may be more heavily loaded than the other. This disparity in weight distribution can result in a tilt towards the more heavily loaded side during flight. The flexibility in sensor placement afforded by the cables extending from the flight computer allows for sensors to be positioned in a range of locations. To this end, a tube has been printed for the ejection charge to go through it and for placing the Raspberry, battery, IMU and pressure sensor. Also mounts have been developed to facilitate the positioning of the camera and GPS, thereby ensuring balance and preventing the rocket from tilting during flight. At the top and bottom of the tube another design was made that keeps the tube centred and for the bottom part two half circles were printed in order to protect the flight computer from the ejection charge.

### 4.3.1. Placement of Microcontroller and Battery

The flight computer is composed of several components, the heaviest of which are the battery and the Raspberry with the hat, which each weigh 26 grams. These components are positioned at the centre of the rocket. This is also evident in Fig. 20. The Raspberry Pi and the battery’s integration within the rocket is facilitated by the utilisation of tape, a method that ensures its precise placement in the confined space of the rocket.

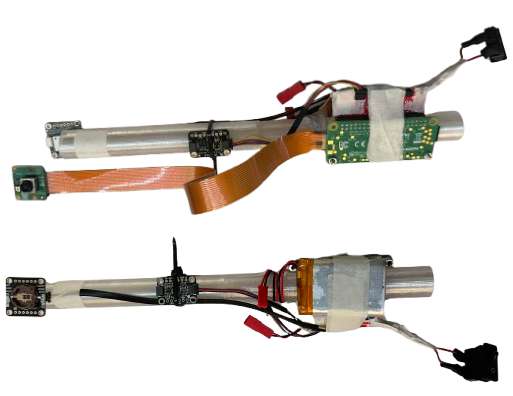
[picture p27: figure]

Figure 20: The tube with the Raspberry Pi and sensors

### 4.3.2. Placement of Sensors and Camera

The sensors of the flight computer are located at a point 10 centimetres above the battery and the Raspberry. The IMU accelerometer and gyroscope, as well as the DPS pressure sensors, are positioned at this location. Both sensors have a weight of 1 gram and in order to keep them in this position tire ups were used. The final sensor is the GPS, which has a weight of 3 grams, and the Raspberry Pi Camera, which also which has a weight of 3 grams. These modules have been placed at a height of 6 centimetres above the IMU and DPS sensors. As the camera has to be mounted on the body tube in order to have a view of outside of the rocket as demonstrated in Fig. 21. Each corner of the modules is equipped with four holes, enabling them to be positioned on the holes of the body, together with a screw and a nut for safety. Furthermore, a hole was made in the body tube of the rocket to accommodate the camera lens, enabling the external environment to be filmed.

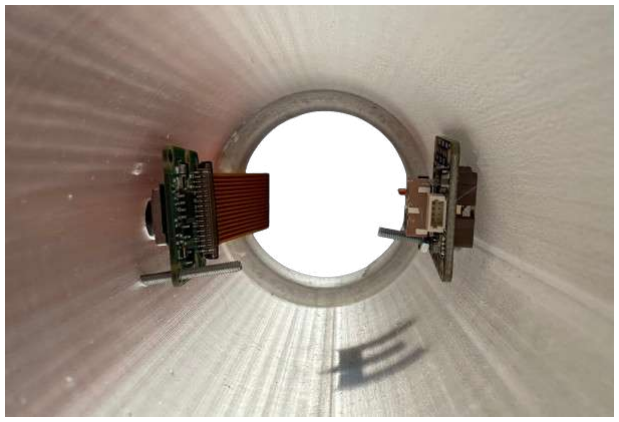
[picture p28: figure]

Figure 21: Camera and GPS

### 4.3.3. Challenges and Design Considerations

Mounting the rocket’s sensors in the best position was a challenge, primarily due to their compact size and the need for lightweight mounts. Furthermore, the need for air to flow freely through the body tube in order to deploy the parachute via the ejection charge was a crucial factor. Initially, the concept of employing oversized mounts that would allow the sensors to slide along the side of the mount was considered. However, these mounts proved to be very heavy. Subsequently, the idea was to use the small holes in the corners of the sensors, with the use of the 3D printer. However, as these mounts were too small, they were prone to breaking. Ultimately, the decision was made to use screws, ensuring precise thickness, to achieve the desired outcome.

### 4.4. Telemetry System

The telemetry system is an important part of the Hermes rocket, facilitating real-time monitoring and post-flight analysis of critical flight data. There will be the possibility to transmit live data from onboard sensors to a ground station for the first few meters of the launch, before the Raspberry pi will disconnect from the Wi-Fi. The telemetry system is essential as it provides insight into the rocket’s performance during the launch, flight, and recovery phases. This is of great importance to the project, as after the launch potential issues can be analysed and then changed before the next flight.

### 4.4.1. Live Data Transmission and Communication

In order to facilitate the transmission of sensor data to the ground station, an intermediate component is required. This component is the Raspberry Pi, which possesses the capability to transmit data via Wi-Fi or Bluetooth, in our case the Wi-Fi option was used. The Raspberry Pi’s integrated code for data collection from the sensors also incorporates the command to transmit the data to the ground station, which has a dedicated code for this purpose, provided both devices are connected to the same Wi-Fi network. The functionality is further enhanced by the use of a mobile hotspot, as the launch site does not have Wi-Fi. After the Rocket, essentially the Raspberry Pi is out of reach from the mobile hotspot, the script will continue to run, meaning it will still store the data to the micro SD that is placed in the Raspberry.

### 4.4.2. Data Logging, Visualization, and Ground Station Integration

The ground station, in this case, a MacBook, receives real-time data transmitted via Wi-Fi from the Raspberry Pi flight computer using the User Datagram Protocol (UDP). This integration enables the live monitoring of flight parameters such as altitude, temperature, velocity, acceleration, vertical speed, orientation (pitch, roll yaw), rotation rate and finally rocket drift, providing immediate feedback to ensure mission success. Furthermore, the ground station processes and visualizes this data using custom Python scripts and libraries like Matplotlib, offering intuitive plots that facilitate real-time decision-making and post-flight analysis.

As illustrated in Fig. 22, the telemetry comprises a total of eight plots. The Temperature vs Time plot displays the onboard ambient temperature measured degrees Celsius and recorded by the the DPS310 pressure sensor. Next to it is the Altitude vs Time in both barometric and GPS. It compares the altitude estimated from the barometric sensor again measured in metres and calculated based on pressure while on the same plot we can also determine the altitude from the GPS sensor. The last plot on the top row is the Vertical Velocity vs Time plot, which computes the rate of change of barometric altitude between samples, offering us an insight into the rocket’s ascent and descent dynamics. In the second row, we can see the Total Acceleration vs Time plot, which tracks the net acceleration magnitude that the rocket is experiencing, which is also derived from the IMU’s accelerometer. Next to this is the Vertical Acceleration vs Time plot which shows only the z-axis acceleration component from the IMU. Finally on the second row is the Orientation vs Time plot, which illustrates the angular orientation of the rocket, derived from the IMU’s accelerometer. On the last row is the Angular Rates vs Time plot which hows the real-time rotational speed (pitch rate, roll rate, yaw rate) measured by the gyroscope. Finally the Rocket drift vs Time plot the horizontal displacement of the rocket from the launch point in metres.

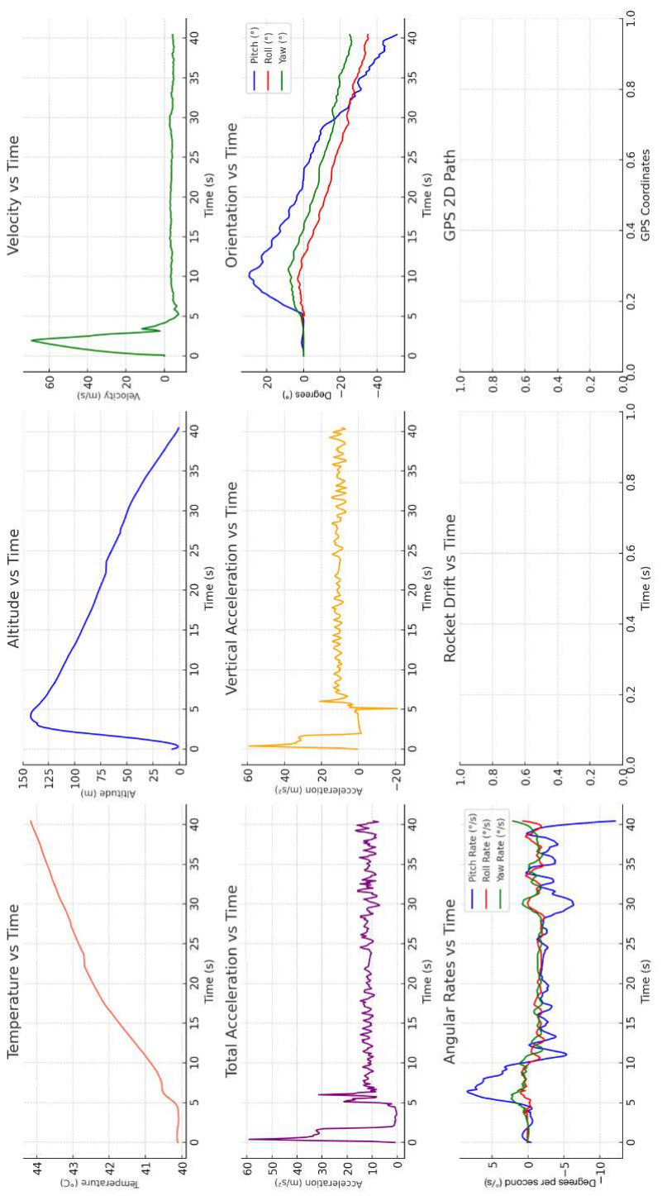
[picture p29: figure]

Figure 22: Data Visualisation

## 5. Propulsion System

### 5.1. Engine Selection and Performance

The selection of the engines had to be compatible with the rocket’s weight, stability margin, target apogee, ejection delay, cost and availability on the market, as well as on the OpenRocket simulator that was used. Given the substantial rocket weight, there was a requirement for powerful engines. Consequently, as a result of the aforementioned considerations, the engines would have to be multiple Klima D-class engines or TSP E-class engines, as the majority of the others are not readily available in Europe. Following a cost-benefit analysis, the Klima D9-5 as shown in Fig. 23 solid rocket engine was selected. This engine has a total impulse of 20 Ns, an average thrust of 9 N, a maximum thrust of 25 N, a propellant weight of 16 g, a burning period of 2.1 s, and a specific ejection delay of 5 s, which ensures the recovery system deploys at apogee. The engine’s dimensions are 70 mm in length and 18 mm in diameter, and a total weight of 27 g, of which 16 g is black powder propellant. A single engine would not be sufficient for the Hermes rocket to overcome Earth’s gravitational pull and also reach the desired apogee of arounf 150 metres. Consequently, the use of three engines would be the optimal configuration [15].

Figure 23: Klima D9-5 engines

### 5.2. Thrust Curve Analysis

The thrust curve of the Klima D9-5 engine is an important factor in determining the rocket’s flight profile. As illustrated in Fig. 24, the engine’s peak thrust of 20 N is attained immediately following the start of the ignition process. This results in a rapid acceleration, enabling the rocket to overcome the forces of gravity and drag. Over the 2.1 s burn duration, the thrust gradually decreases, stabilising at an average of 9.2 N. This smooth thrust profile is conducive to minimising stress on the rocket’s structure while maintaining stability. The total impulse of 20 Ns guarantees that the rocket attains its target apogee under nominal conditions. The Klima D9-5 engine was available directly in the OpenRocket motor library, meaning its predefined thrust curve was used in the simulation. This allowed for more accurate predictions of performance and flight dynamics. The thrust curve analysis also makes sure that the engine provides enough force to maintain a thrust-to-weight ratio greater than 5:1, a critical parameter for safe and stable flight [15].

Figure 24: Thrust Curve of Klima D9-5 Engine [15]

### 5.3. Integration with Rocket Design

The D9-5 engines are mounted in a custom-design engine mount that can be seen in Fig. 25. The mount has been designed in a way that in fits precisely within the body tube where it was then stabilised with the epoxy glue. This, guarantees the alignment of the thrust vector during the launch phase with the rocket’s centre of gravity thereby maintaining stability. In more detail, two engine mounts have been positioned at one and five centimetres from the bottom of the tube. The dimensions of the 3-ring cluster design have an outer diameter of 63.2 mm and a thickness of 5 mm.

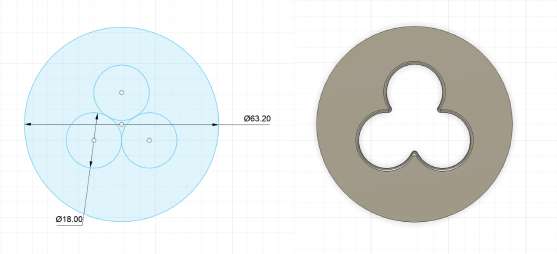
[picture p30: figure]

Figure 25: Engine Mount on Fusion 360

## 6. Rocket Simulation and Stability Analysis

### 6.1. Stability Principles

Stability is an important part in model rockets, it makes sure that the rocket maintains a predictable and controlled flight trajectory while ascending and descending. Having a stable rocket means that it will not deviate from its planned trajectory due to aerodynamic forces, but instead helps it to achieve this trajectory with precision. The three main objectives of the stability analysis are to optimise the rocket’s flight trajectory, to keep it safe and finally to verify that the design parameters are aligned with the aerodynamic criteria. This is achieved by balancing the rocket’s CG and CP to ensure an adequate stability margin, which is commonly expressed in terms of the rocket’s body diameter (Cal). The optimal range for most model rocket is between 1-2 Cal, as it makes sure that it is stable enough under different flight conditions. Stability analysis is instrumental in refining design parameters, such as fin size and placement, or internal component distribution, thereby ensuring the rocket’s capacity to withstand real-world disturbances, including wind and uneven thrust. The incorporation of these principles into the design process enables engineers to enhance performance, mitigate risks, and ensure the success of mission outcomes [16].

### 6.1.1. Centre of Gravity (CG) and Centre of Pressure (CP)

Rocket stability is governed by the relative positions of the CG and CP. When a free body in space rotates, it spins around an imaginary point where all its mass appears to be concentrated, this is the balance point, or else called the centre of gravity. On the other hand the point where all the aerodynamic forces act is called the centre of pressure.

### 6.1.2. Stability Margin and Caliber

Having established the definitions of the CG and CP, the subsequent section will address the consequences of these points on the stability of a model rocket. It should be noted that three distinct stability conditions can be identified, as illustrated in Fig. 26.

1. Positive stability: In this condition, the model rocket’s CG is positioned ahead of the CP. The design of the model rocket is characterised by the presence of large fins set far back on the body tube. This results in the rocket flying straight and weathercocking into the wind at launch.
2. Neutral stability: In this case, the CP and CG are at the same position on the model rocket. This may occur if the rocket has a lightweight nose or fins that are too small, or both. In the absence of stabilising and restoring forces in the model rocket, this may result in unpredictable paths.

3. Negative stability: In this condition, the CG is behind the CP. In this scenario, the aerodynamic forces on the fins tend to cause the model to fly tail-first, which is not possible under power. As the nose has any pitch or yaw movement, a force exists to keep it swinging, resulting in the model pinwheeling end over end and eventually descending to the ground [1].

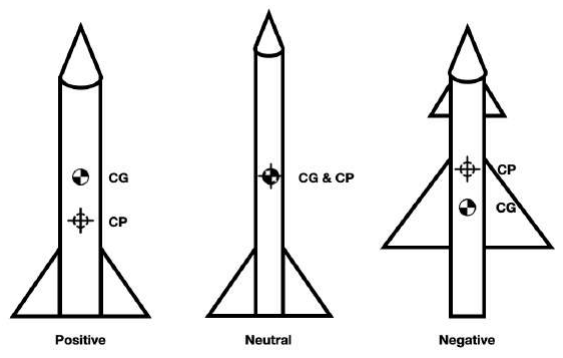
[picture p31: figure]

Figure 26: The three stability conditions with their CG-CP

It is important that the model rocket has the CG ahead of the CP. This is shown in Equation Eq. (28) and it represents the distance between the CG and the CP, expressed in terms of the rocket’s body diameter.

- The definition of the caliber is derived from the following equation:

Cal =

Distance between CG and CP
Body Tube Diameter | (28)

There are four interpretation of Cal values:

- 0 cal: The CG and CP are aligned, thereby rendering the rocket highly unstable. This condition has previously been described as neutral stability.
- <1 cal: The rocket is marginally stable and may not be able to fly in a straight path, particularly when subjected to wind disturbances.
- 1-2 cal: The rocket exhibits ideal stability, which is the optimal range for most model rockets. This condition ensures that the rocket flies straight while maintaining sufficient manoeuvrability.
- >2 cal: The rocket may exhibit excessive stability, thereby impeding the process of adjustment and potentially resulting in a deviation from the intended trajectory in the presence of strong winds [16].

The location of the CG and CP of the Hermes rocket can be determined by observing the OpenRocket application. Specifically, from the tip of the rocket, the CG is situated at 570 mm and the CP is at 703 mm. This shows that the Cal value is 1.98, suggesting that the rocket maintains ideal stability and would only deviate from its trajectory in the presence of strong winds.

### 6.2. Weight Distribution

As previously mentioned it is vital to make sure there is optimal weight distribution within a rocket, in order to maintain stability and ensure the rocket follows the intended flight path without deviating excessively to either side due. In order to achieve this, the sensors and all other mass components within the rocket are placed in equal positions. This has been achieved based on the weight of each sensor and then by placing them opposite each other so they can cancel out as depicted in Fig. 27. To illustrate this approach, the IMU and the DPS310, both of which weigh 1 gram. A similar principle applies to the Camera and GPS, which each weigh 3 grams. The battery and the Raspberry, on the other hand, have weights of 26 grams each. However, the Raspberry also contains the step-up converter and the rocker switcher, which powers the flight computer. These components cancel out the weight difference. The engines are another component that is very heavy, with a total mass of 81 grams, but with the help of the engine mounts, they are positioned centrally. The adapters that connect the body tubes together are in total three, but they are placed in equal distances. Finally, the parachute, which is of equal width to the body tube, is located in close proximity to the first adapter, thus ensuring a centralised positioning of the system.

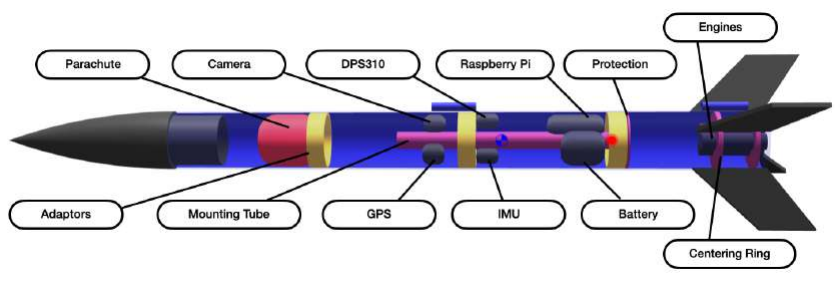
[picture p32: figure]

Figure 27: Weight Distribution

### 6.3. OpenRocket Documentation and Justification of Simulation Differences

### 6.3.1. How OpenRocket Works and Its Assumptions

The OpenRocket software was utilised for the purpose of simulating the flights of the rocket. OpenRocket is an open-source software that can be used for model rocket simulators. It facilitates the design and simulation of rockets prior to construction and launch. The utilisation of simulations enables the prediction of key parameters, optimisation of rocket design and assessment of conditions such as weight distribution, engine clusters, and parachute deployment, with the objective of determining their impact on the overall flight plan. These simulations are founded on aerodynamic theories and numerical methods to predict the rocket’s flight characteristics. A more detailed analysis of the architecture of OpenRocket reveals that it is build as a modular Java system that has core functionalities like graphical user interface, the simulation engine as well as aerodynamic calculators, which are split into dedicated software package. These details have been extensively described in Development of an Open Source model rocket simulation software a master’s thesis by Sampo Niskanen [5]. Rocket designs are represented through a component-based structure, in which each component like the nose cone, body tube, or fins is defined as a subclass of the abstract Rocket Component class. This structural design produces a tree-like model that replicates the physical rocket design, with additional interfaces such as Motor Mount and Clusterable allowing for the flexible modeling of multi-motor clusters and staging setups. Additionally, OpenRocket uses reflective programming techniques in order though to maintain modularity. The software design is structured in a way that the system is both adaptable and efficient, thereby supporting a wide variety of rocket configurations and simulation scenarios. The component architecture is illustrated in the diagram presented in Fig. 28.

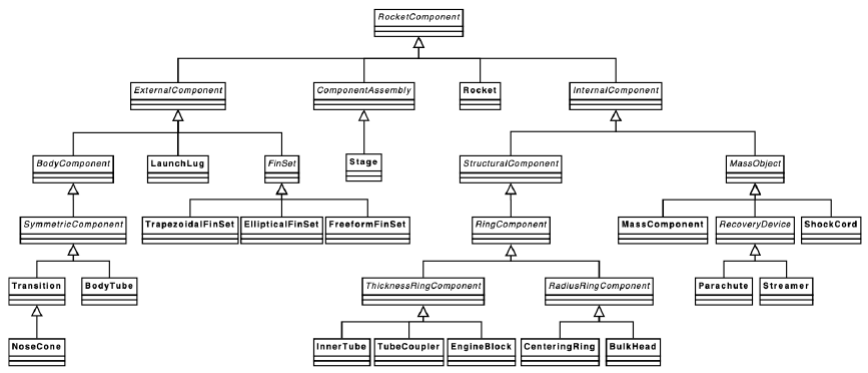
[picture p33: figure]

Figure 28: A diagram of the rocket component classes [5]

Furthermore, except for the core functionality of OpenRocket that it offers, it is also designed to be modular. As previously mentioned, the modular Java System allows the advanced users to add new aerodynamic models or simulation methods like swapping Runge-Kutta for Euler integration or incorporating CFD, without the need of rewriting the whole system. Additionally, another feature is the use of simulation listeners that are able to interact with the simulation in real time. They have the ability to monitor flight progress, collect custom data as well as modify the rocket’s properties while in simulation, thus making possible to test active control systems. All these features make OpenRocket not only a design tool but also a flexible platform for research and advanced experimentation.

### 6.3.2. Core Equations and Calculation Methods

As outlined in the master’s thesis Development of an Open Source model rocket simulation software by Sampo Niskanen [5], the three core equations implemented in OpenRocket are presented below. These include the stability calculation using the Barrowman equations Eq. (29), the drag force estimation Eq. (30), Eq. (31), and the motion simulation based on the 4th-order Runge-Kutta method Eq. (32).

1. Stability Calculations:
The initial step in this process is to consider the core equations and calculation methods that are utilised by OpenRocket. For instance, the stability of a rocket is determined by the Barrowman equations. These equations calculate the centre of pressure based on the geometry and configuration of the rocket components. There is no external database utilised in this scenario, Instead, OpenRocket employs real-time calculation of the centre of pressure (CP) and centre of gravity (CG) from the rocket’s input geometry. The normal force coefficient derivatives CNa for each component are estimated using analytical formulas derived from the Barrowman method, and subsequently summed as:

XCP =

P

XiCNa,i
P

CNa,i

(29)

- Where:

– Xi

is the position of the component’s centre of pressure.

– CNa,i is the normal force coefficient derivative for the component.

2. Drag Force Estimation:
As is the case in the Hermes project, the rocket reaches only subsonic speeds (Mach < 0.8). Therefore, to calculate the drag force, OpenRocket uses the classical equation:

FD =

1
2
ρu²CDA | (30)

Where the total drag coefficient CD is calculated by summing individual contributions:

CD = CDbody + CDfin + CDbase + CDparasitic | (31)
- Where:

– CDbody is the drag from the body tube.

– CDfin is the drag from the fins.

– CDbase is the drag from the base due to low-pressure zones.

– CDparasitic is the drag from the launch lugs or other small protrusions.

The estimated values for each component are obtained using empirical data from wind tunnel experiments and established aerodynamic tables, based on slender-body assumptions derived from the Barrowman method. As the Hermes rocket operates entirely within the subsonic regime, supersonic and transonic corrections are not applied here.

3. Motion Simulation:
In relation to the motion simulation, the rocket flight is simulated by employing the 4th-order Runge-Kutta method to solve the equations of motion. But in this case OpenRocket relies on external data. Specifically, the thrust curves come from a database such as thrustcurve.org [15] which provide time vs. thrust profiles based on manufacturer or measured data. Additionally, the mass depletion is calculated based on total propellant mass and burn time from the motor file and finally it uses default atmospheric condition, unless the uses inputs custom values.

The core equation is as follows:

d

2x
dt²

=

Fthrust − Fdrag − Fgravity
m

(32)

- Where:

– Fthrust is the thrust force from the engine.

– Fdrag is the air resistance or drag force.

– Fgravity is the gravitational force.

– m is the rocket mass, which decreases over time as the fuel burns.

### 6.3.3. Simulation Assumptions

The core equations and calculation methods alone are insufficient to yield the final result, and consequently, OpenRocket also bases its simulations on a combination of aerodynamic theories and numerical methods, incorporating several assumptions to simplify and optimise the simulation process. Firstly, the rocket is assumed to be axially symmetric. This assumption simplifies the calculations by presuming that the aerodynamic forces are uniformly dispersed along the rocket’s axis. This is a common assumption in the majority of traditional rocket designs, where the fins and body components exhibit symmetry. In the context of ideal motor performance, the motor thrust is modelled based on thrust curves provided by the manufacturer. These curves represent optimal conditions and do not consider environmental variations, such as temperature. Consequently, minor discrepancies may emerge in the motor performance predictions. Additionally, OpenRocket simplifies the complex behaviour in the transonic and supersonic regimes by using predefined drag coefficients, thus facilitating high-speed aerodynamics. Unless modified by the user to reflect actual launch conditions, the simulations assume standard atmospheric conditions. Another assumption that, unless explicitly defined, are the wind conditions and turbulence, which are not factored into the simulation. However, these can be changed if the relevant data are available [5]. Finally, for the recovery phase like the parachute deployment in the case of this project, OpenRocket models it as an event triggered stage where the drag coefficient is getting increased significantly during deployment. The user has the option to input the drag coefficient and effective surface area manually or to select from default preset values in order to model the parachute’s drag. In contrast to the thrust curves that rely on external motor databases, the parachute functions independently. When the parachute is deployed, the simulation tracks the descent phase by calculating the new drag values and recalculating the rocket’s deceleration, descent rate, and terminal velocity accordingly.

### 6.3.4. OpenRocket Simulation Features and Output Parameters

In order to achieve the most accurate simulations on OpenRocket, it is possible to input parameters such as launch conditions, aerodynamic properties, and propulsion data. Following this, the user has the option to generate various plots, including the final trajectory, acceleration and forced acting on the rocket, drag coefficient vs Mach number, parachute deployment sequence and descent rate, and stability metrics such as CG and CP over time. It has been demonstrated that OpenRocket predictions, when substantiated by experimental validation, exhibit an accuracy of 10-15 percent relative to real flight data. Variations in performance are attributed to wind effects, surface irregularities, and discrepancies in motor performance.

### 6.3.5. Possible Reasons for Differences

Additionally to the experimental factors, the simulation model includes also assumptions and uncertainties. Specifically, the aerodynamic models assume axisymmetric, rigid-body rockets with smooth surfaces, neglecting the influence of manufacturing imperfections, surface roughness, or minor misalignments. In addition, environmental conditions such as wind and turbulence are only used if the user inputs them, in all other cases, the simulation utilises default settings that do not allow for site-specific variation. Moreover, the motor performance is simulated by using the ideal thrust curves, as previously described in Section 5.2, and does not account for temperature effects, nozzle erosion, or inconsistencies in ignition. These parameters cannot be adjusted or inputted at a later stage in the OpenRocket simulation. Another important note is that the empirical drag coefficients that are being used are derived from simplified fittings and therefore lack the ability to accurately capture complex fluid dynamics such as turbulent wakes or Reynolds number sensitivity. A summary of the key simulation assumptions and their potential impacts is provided in Table 3. Overall, these assumptions introduce systematic variations, which can result in discrepancies between simulated predictions and actual flight performance [5], [16].

Category | Assumption | Potential Impact
Rocket Geometry | Axisymmetric, rigid-body rockets with smooth surfaces | Ignores flexing, warping or off-center mass
Aerodynamic Modeling | Uses empirical drag coefficients from slender-body models | Not accounting for turbulent wakes or surface texture
Motor Performance | Uses idealised thrust curves from databases | Not accounting for temperature, nozzle wear, or misfire
Atmospheric Conditions | Assumes standard atmosphere (unless user inputs custom data) | Ignores site-specific wind, temperature, or pressure
Recovery Modeling | Applies user-specified or default parachute parameters | Errors in drag coefficient or area affect descent rate
Numerical Integration | Uses 4th-order Runge-Kutta with fixed time-step | Small numerical errors may accumulate over long flights

Table 3: Summary of key simulation assumptions in OpenRocket and their potential impacts on accuracy

## 7. Recovery System Design

The recovery of the rocket in an intact state is of great importance in this project, as the rocket is required to be able to fly multiple times and it would also prevent any damage to the flight computer. In this particular project, the parachute recovery system has been selected. This recovery was first used in model rockets by Orville H. Carlisle in 1954, and since then there has been a great deal of research into parachutes, with these systems still being used in many cases today. The parachute is affixed to the rocket’s nose cone, and in conjunction with a shock cord, it constitutes a highly reliable recovery system [1].

### 7.1. Parachute Design for Safe Descent Rate

Parachutes are available in a variety of shapes, including circular, square, hexagonal, and octagonal designs. The prevalence of circular parachutes is low, as the fabrication process for hexagonal and octagonal parachutes is more straightforward. The parachute’s design incorporates a targeted descent rate of 4-6 m/s to ensure a safe and controlled descent while also keeping an easy design using a semi-spherical octagonal. This rate is calculated to minimise the risk of damage to the rocket during landing while ensuring a timely recovery. The diameter of the parachute was calculated using the drag equation, as shown in Eq. (33), Eq. (34), and Eq. (35), with a resultant measurement of 77 cm [1].

- The drag equation is calculated as:

D = W = 0.5 · ρ · V

2
- Cd · A | (33)
- Where:

– W is the rocket’s weight.
– ρ is the air density, which at sea level is typically 1.225 kg/m³

– V s the desired descent velocity.

– Cd is the drag coefficient, which for a hemispherical parachute is approximately 1.5.

– A is the parachute’s area.

In greater detail, the parachute area is calculated as follows [17]:

A = π

d
2

!2
=

πd²
4

(34)

### 7.2. Material Selection, Size, and Deployment Mechanism

The parachute has a fabric that is super soft, light and tear-resistant quality. The parachute’s design incorporates eight shock cords, which contribute to its structural integrity. These cords are engineered to possess both tensile strength and resistance to heat from the ejection charge.

- Plugging the area into the drag equation and solving for d, we get:

d =

s
8 · m · g
π · ρ · V
2
- Cd

(35)

The dimensional calculations were determined by the total mass and the desired descent rate. The shock cord, a synthetic material characterized by its elastic properties, was segmented into two sections: 60 cm from the body tube to the nose cone, and 6 cm from the swivel to the parachute itself as it can be seen in Fig. 29. This configuration was selected to minimize stress on the attachment points. The deployment of the parachute is contingent upon the utilization of a black powder ejection charge within the engines, which functions to disengage the rocket’s nose cone from the body tube at apogee. This enables the parachute to be deployed. The system is initiated by the five-second delay inherent in the engines, a concept elaborated upon in Section 5. Prior to the integration of a swivel mechanism in the design, measures were implemented to avert the entanglement of the parachute chords during descent, thereby ensuring a seamless and regulated recovery.

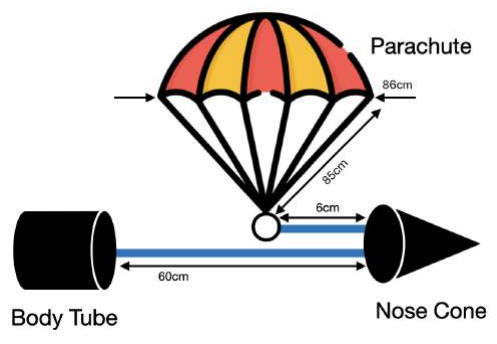
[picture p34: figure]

Figure 29: The parachute system with dimensions

## 8. Testing and Validation

As with all aerospace missions, there are some requirements that have to be set first and tests are designed to verify that each requirement is met. These requirements are about the rocket, the flight computer, the parachute and telemetry. Specifically, they ensure that the flight computer and sensors function correctly in the expected environment. The rocket structure is aerodynamically stable, the parachute recovery system deploys reliable and finally the telemetry systems stores flight data without significant or any losses.

ID | Requirement Description | Verification Method
R-1 | The flight computer shall collect sensor data (pressure, altitude, temperature, GPS, accelerometer, gyroscope, magnetometer) at a minimum rate of 1 Hz | Sensor data logging test
R-2 | The flight computer shall store data over a distance of at least 200 metres | Telemetry transmission range test
R-3 | The camera shall store video feed over a distance of at least 200 metres | Video Camera storing range test
R-4 | The parachute shall eject and deploy upon activation of the ejection system charges | Drop test and ejection test
R-5 | The power system shall operate for at least the entire mission duration (15 minutes) | Battery endurance test
R-6 | The aerodynamic stability margin shall be within ≥ 1.5 cal (calibers) to ensure a stable flight trajectory | Swing test

Table 4: Requirement Description and Verification Method

### 8.1. Pre-Flight Electronics Validation

Starting with the sensor data, telemetry transmission and camera test (R-1, R-2, R-3) as they can be verified simultaneously. The objective is to verify that the sensors record accurate data and the Raspberry Pi shall store data and the camera stores video feed while it is at least over 200 metres away from the ground station (which is the laptop). The procedure here is:

1. Power on the flight computer and connect it via ssh to a laptop.
2. Set up the Raspberry Pi for live data transmission and the camera.

3. Record sensor data and video feed while the system remains stationary.
4. Walk away from the ground station at increasing distances.
5. Complete the data collection and switch off the Raspberry Pi.
6. Check for data loss.

In order for the requirement to be successful the data should be recorded at ≥ 10 Hz and that there is a stable transmission at 200 metres with minimal to no data loss. On 20 March 2025, the test was successfully conducted by initially utilising live telemetry for the initial 60 metres, followed by the relocation of the flight computer after its disconnection from the Wi-Fi network and subsequent power interruption. Upon reconnection, it was determined that the flight computer continued to store data up at 1 Hz to the point of the power interruption and the video feed was saved successfully. Additionally this test was conducted every time before each flight.

### 8.2. Launch and Recovery Testing

In this test the objective is to ensure that the parachute eject and deploys successfully (R-4). The procedure would be:

1. Place the parachute and ejection system in the rocket.
2. Activate the parachute ejection charge.
3. Monitor the parachute deployment.

For the test to be successful, the parachute must deploy successfully. On March 26, 2025, the parachute was folded in accordance with the established protocol, prior to its deployment on the rocket. The parachute was then ejected by blowing air into the rocket, where the actual ejection charge will be located.

### 8.3. Battery Endurance Test

In this case the objective is the that the power system supports the mission duration (R-5). The procedure for this test is:

1. Fully charge the battery system.
2. Run the entire flight computer system, sensors, and transmission module for at least 15 minutes.
3. Monitor the battery over time to detect any disconnections.

For the test to be successful the system shall operate continuously. On March 21, 2025, the battery was first fully charged, then the GPS test was conducted, which is the test for the GPS to connect to a satellite for 15 minutes and after that the scripts that will also be used at the launch were ran, which are the data storing and video storing for another 10 minutes.

### 8.4. Ground Testing of Aerodynamic stability Test

Continuing with the aerodynamic stability (R-6) the objective here is that the rocket’s stability margin is ≥ 1.5 calibers. This would be tested with a swing test. The procedure is:

1. Find the rocket’s CG.
2. Attach a string to the CG and spin it to check for stable flight behaviour.

As here it would be difficult to check the exact caliber number the pass criteria would be that the rocket maintains a stable flight path during the test. Before each flight this test was conducted to ensure the weight distribution was correct.

## 9. Results and Discussion

### 9.1. Overview of Test Flights

In total, there were 12 engines and as three engines are required per launch there were overall four launches to evaluate the rockets flight performance, to access the sensors reliability and finally to validate the accuracy of the simulation predictions in OpenRocket. The goal of each flight was to capture data such as temperature, barometric altitude, GPS altitude, velocity, vertical speed, acceleration magnitude, orientation (pitch, roll, yaw), rotation rate, and GPS path. All the sensors on the flight computer were thoroughly tested prior the launch as discussed in previous sections. In Table 5, the conditions and weather data of each flight are summarized; these environmental parameters were also input into the simulation to improve prediction accuracy. This process improved the predicted descent rates and flight durations, which showed that even small corrections to environmental and propulsion parameters can significantly improve the reliability of the simulation outputs.

Parameter | Flight 1 | Flight 2 | Flight 3 | Flight 4
Launch Date | 05.04.2025 | 18.04.2025 | 04.05.2025 | 11.05.2025
Launch Site Elevation | 35 m | 2 m | 175 m | 19 m
Temperature | 19 °C | 17 °C | 22 °C | 15 °C
Atmospheric Pressure | 994.47 hPa | 1012.55 hPa | 991.93 hPa | 1015.64 hPa
Relative Humidity | 55 % | 60 % | 45 % | 68 %
Wind Speed | 15 km/h | 7.2 km/h | 11 km/h | 7 km/h
Wind Direction | 258 ° | 120 ° | 201 ° | 144 °

Table 5: Flight Conditions and Environment Summary

### 9.2. Flight Data Analysis

This section presents the results of each flight, which were then compared with the simulation data. In the subsequent section, a comparison is drawn between the altitude, velocity, vertical speed, and acceleration magnitude plots, as these are the only variables that can be simulated. The remaining plots are either not available for simulation, as is the case with the temperature inside the rocket, or OpenRocket assumes ideal vertical flight, thus resulting in the absence of 6 Degrees Of Freedom (DOF) attitude or in-flight dynamics.

### 9.2.1. Flight 1: Data overview

Flight 1 was conducted on April 5, 2025. As illustrated in Fig. 31, the complete set of telemetry plots acquired from the first flight is presented. The visualisation of these plots, which utilises a 1 Hz sampling rate, offers a comprehensive representation of the rocket’s behaviour throughout all phases of its flight trajectory. Before the flight we can see clearly that the GPS did not lock with a satellite and there were no data, meaning the GPS path and the Rocket drift plots are not available. The rocket launches immediately and hits the ground at 30 s. Starting with the temperature plot, we can see that it starts at around 42.5 °C. This temperature is likely the result of internal heating or the influence of nearby electronics. The temperature rises to a peak of around 50 °C during the ejection charge. It is evident at this point that the heat has penetrated the protection system and transferred to the flight computer. The vertical velocity shows a sharp spike at the launch, then peaking at around 2 s with 42 m/s and then a clear drop that shows the parachute deployment and at 30 s it stabilises showing that the rocket hit the ground. In terms of vertical and total acceleration, there is a spike at the start, peaking at around 2 s and reaching 22 m/s² for total acceleration and around 15 m/s²
for the vertical acceleration. As for the orientation plot, the pitch shows significant changes in the rockets nose angle, especially during the ascent part, as for roll it fluctuates more consistently showing some imbalance or aerodynamic forces and finally yaw remains relatively stable, with minor adjustments in heading. All three lines after 12 s stabilise, showing steady flight after ascent and recovery deployment. Finally about the angular rates plot, pitch again shows sharp fluctuations at launch, the roll rate has some periodic fluctuations probably due to recovery dynamics and lastly the yaw rate has smaller vibrations that the other two. As illustrated in Fig. 30, the last frame of the camera is visible. The issue here was that the camera was disconnected from the Raspberry Pi, which additionally was terminally damaged by the ejection charge penetrating the protection system. Consequently, it was necessary to design an improved protection system for the next flight.

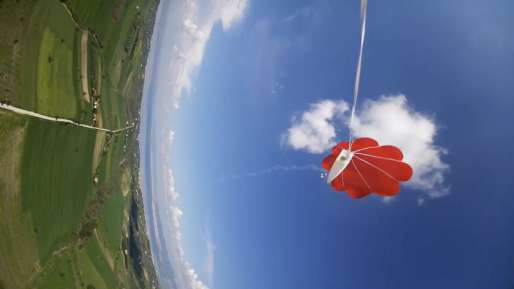
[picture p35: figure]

Figure 30: On-Board photo from Flight 1

Figure 31: Telemetry data from the first flight

Prior to conducting a more detailed examination of the plots, it is important to acknowledge that the sampling rate was inadequate, potentially resulting in the highest point of any data set occurring between two samples. The altitude plot in Fig. 32, where the blue line represents the actual altitude achieved by the rocket and the red line represents the simulated altitude in OpenRocket, demonstrates that the simulated apogee was not attained due to the aforementioned reason. Additionally, the rocket’s landing may have been delayed due to strong winds, which would be consistent with the observed data.

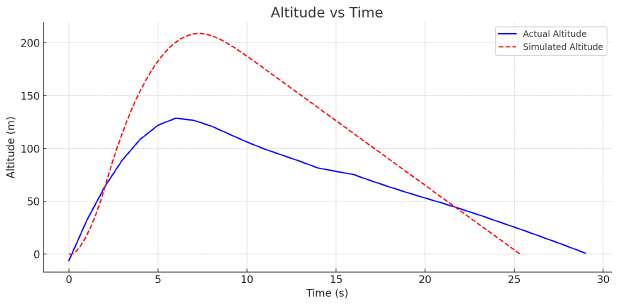
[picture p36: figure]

Figure 32: Flight 1 - Comparison of Actual and Simulated Altitude

As demonstrated in Fig. 33, the velocity plot reveals that the peak in the simulation occurs at approximately 55 m/s, while the peak in the actual plot is around 45 m/s. Following the deployment of the parachute, there was a substantial decrease in velocity, with the minimum vertical velocity being -12.5 m/s in the simulation, at which point it stabilises. In the actual plot, the minimum vertical velocity is -10 m/s, but it fluctuates slightly. The difference between the two plots may be due to sampling rate, uneven deployment of the parachute, or irregularities in air resistance.

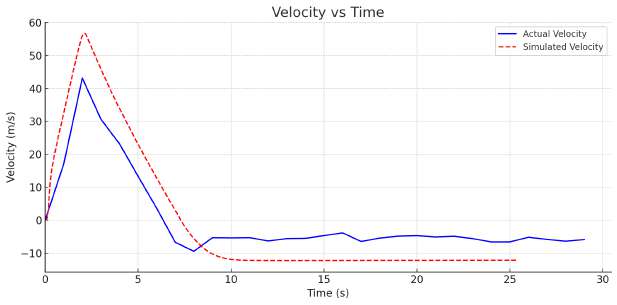
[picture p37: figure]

Figure 33: Flight 1 - Comparison of Actual and Simulated Velocity

Finally, with regard to the acceleration plots in Fig. 34, it should be noted that the actual data represents apparent accelerations, i.e., accelerations without gravity subtracted. This ensures that the acceleration curves peaks closer to the presentation of net forces by OpenRocket. However, it should be noted that the peak acceleration values in the actual data may differ from the simulation due to real-world effects such as sensor sampling limitations, and because the highest recorded values could have occurred between two samples. In more detail both plots for the simulated data follow a smoother trend, with sharp peaks at key events but in the actual data there are more fluctuations. Furthermore, for the simulated total acceleration there are some relative steady values after the burnout but on the other hand the actual total acceleration has significant variation in later stages. This is likely caused by forces such as wind or slight deviations in the flight path.

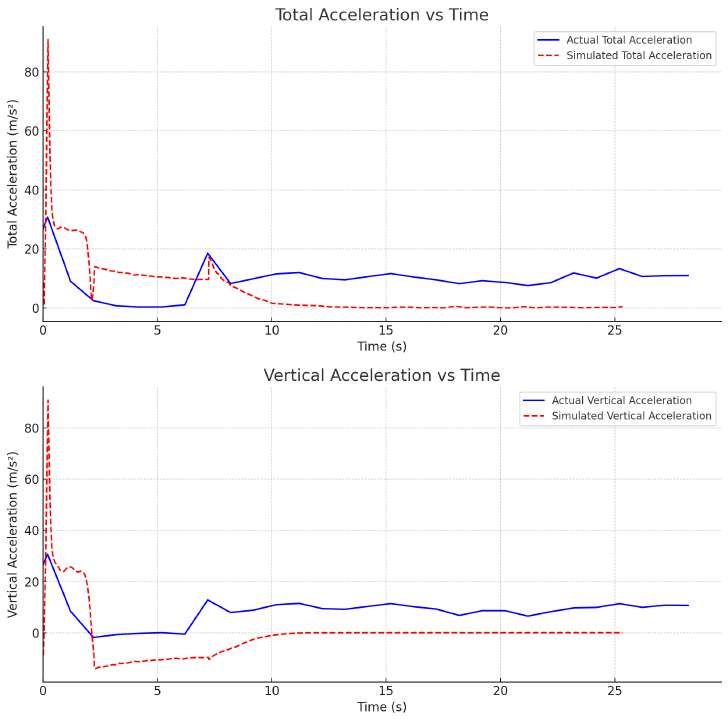
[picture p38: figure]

Figure 34: Flight 1 - Comparison of Actual and Simulated Total and Vertical Accelerations
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

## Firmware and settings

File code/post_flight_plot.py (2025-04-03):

import pandas as pd
import matplotlib.pyplot as plt
import matplotlib.animation as animation
from math import sqrt, atan2, degrees

# Load the CSV
df = pd.read_csv("/Users/filpas/Downloads/csv.csv")  # <--- Change this path to your CSV file

# Simulated time (1Hz)
df["Time"] = range(len(df))

# Initial calibration values
initial_total_acc = sqrt(df["Accel_X (m/s²)"][0]**2 + df["Accel_Y (m/s²)"][0]**2 + df["Accel_Z (m/s²)"][0]**2)
initial_vertical_acc = df["Accel_Z (m/s²)"][0]
initial_roll = degrees(atan2(df["Accel_X (m/s²)"][0], sqrt(df["Accel_Y (m/s²)"][0]**2 + df["Accel_Z (m/s²)"][0]**2)))

# Derived telemetry values
df["Total_Acceleration"] = df[["Accel_X (m/s²)", "Accel_Y (m/s²)", "Accel_Z (m/s²)"]].apply(
    lambda row: sqrt(row.iloc[0]**2 + row.iloc[1]**2 + row.iloc[2]**2), axis=1) - initial_total_acc
df["Vertical_Acceleration"] = df["Accel_Z (m/s²)"] - initial_vertical_acc
df["Vertical_Velocity"] = df["Altitude (m)"].diff().fillna(0)
df["Pitch"] = df[["Accel_X (m/s²)", "Accel_Y (m/s²)", "Accel_Z (m/s²)"]].apply(
    lambda row: degrees(atan2(row.iloc[1], sqrt(row.iloc[0]**2 + row.iloc[2]**2))), axis=1)
df["Roll"] = df[["Accel_X (m/s²)", "Accel_Y (m/s²)", "Accel_Z (m/s²)"]].apply(
    lambda row: degrees(atan2(row.iloc[0], sqrt(row.iloc[1]**2 + row.iloc[2]**2))), axis=1) - initial_roll
df["Yaw"] = df[["Accel_X (m/s²)", "Accel_Y (m/s²)", "Accel_Z (m/s²)"]].apply(
    lambda row: degrees(atan2(row.iloc[2], sqrt(row.iloc[0]**2 + row.iloc[1]**2))), axis=1)

# Angular rates (swapped to match live telemetry)
df["Pitch_Rate"] = df["Gyro_X (°/s)"]
df["Roll_Rate"] = df["Gyro_Y (°/s)"]
df["Yaw_Rate"] = df["Gyro_Z (°/s)"]

# Rocket drift
df["Rocket_Drift"] = df.apply(
    lambda row: sqrt((row["GPS_Latitude"] - df["GPS_Latitude"][0])**2 +
                     (row["GPS_Longitude"] - df["GPS_Longitude"][0])**2) * 111139,
    axis=1)

# Setup figure
fig, ax = plt.subplots(3, 3, figsize=(16, 12))
ax = ax.flatten()

titles = [
    "Temperature vs Time", "Altitude (Barometric & GPS) vs Time", "Vertical Velocity vs Time",
    "Total Acceleration vs Time", "Vertical Acceleration vs Time", "Orientation (Pitch, Roll, Yaw) vs Time",
    "Angular Rates (°/s) vs Time", "Rocket Drift vs Time", "GPS 2D Path"
]

ylims = [
    (0, 50), (0, 250), (-12.5, 60),
    (0, 90), (-15, 90), (-180, 180),
    (-25, 40), (0, 500), None
]

for i in range(9):
    ax[i].set_title(titles[i])
    if ylims[i]: ax[i].set_ylim(*ylims[i])
    ax[i].grid(True)

# Set GPS plot limits
lat_min, lat_max = df["GPS_Latitude"].min(), df["GPS_Latitude"].max()
lon_min, lon_max = df["GPS_Longitude"].min(), df["GPS_Longitude"].max()
if lat_min == lat_max: lat_min -= 0.0001; lat_max += 0.0001
if lon_min == lon_max: lon_min -= 0.0001; lon_max += 0.0001
ax[8].set_xlim(lat_min, lat_max)
ax[8].set_ylim(lon_min, lon_max)

# Plot lines
lines = {
    "temperature": ax[0].plot([], [], label="Temperature (°C)", color="red")[0],
    "alt_baro": ax[1].plot([], [], label="Barometric Altitude (m)", color="blue")[0],
    "alt_gps": ax[1].plot([], [], label="GPS Altitude (m)", color="red")[0],
    "velocity": ax[2].plot([], [], label="Vertical Velocity (m/s)", color="green")[0],
    "total_acc": ax[3].plot([], [], label="Total Acceleration (m/s²)", color="purple")[0],
    "vertical_acc": ax[4].plot([], [], label="Vertical Acceleration (m/s²)", color="orange")[0],
    "pitch": ax[5].plot([], [], label="Pitch (°)", color="blue")[0],
    "roll": ax[5].plot([], [], label="Roll (°)", color="red")[0],
    "yaw": ax[5].plot([], [], label="Yaw (°)", color="green")[0],
    "pitch_rate": ax[6].plot([], [], label="Pitch Rate (°/s)", color="blue")[0],
    "roll_rate": ax[6].plot([], [], label="Roll Rate (°/s)", color="red")[0],
    "yaw_rate": ax[6].plot([], [], label="Yaw Rate (°/s)", color="green")[0],
    "drift": ax[7].plot([], [], label="Rocket Drift (m)", color="brown")[0],
    "gps_path": ax[8].plot([], [], label="Path")[0],
}

for a in ax:
    a.legend()

# Update animation
def update(frame):
    t = df["Time"][:frame+1]
    lines["temperature"].set_data(t, df["Temperature (°C)"][:frame+1])
    lines["alt_baro"].set_data(t, df["Altitude (m)"][:frame+1])
    lines["alt_gps"].set_data(t, df["GPS_Altitude (m)"][:frame+1])
    lines["velocity"].set_data(t, df["Vertical_Velocity"][:frame+1])
    lines["total_acc"].set_data(t, df["Total_Acceleration"][:frame+1])
    lines["vertical_acc"].set_data(t, df["Vertical_Acceleration"][:frame+1])
    lines["pitch"].set_data(t, df["Pitch"][:frame+1])
    lines["roll"].set_data(t, df["Roll"][:frame+1])
    lines["yaw"].set_data(t, df["Yaw"][:frame+1])
    lines["pitch_rate"].set_data(t, df["Pitch_Rate"][:frame+1])
    lines["roll_rate"].set_data(t, df["Roll_Rate"][:frame+1])
    lines["yaw_rate"].set_data(t, df["Yaw_Rate"][:frame+1])
    lines["drift"].set_data(t, df["Rocket_Drift"][:frame+1])
    lines["gps_path"].set_data(df["GPS_Latitude"][:frame+1], df["GPS_Longitude"][:frame+1])
    for i in range(8):
        ax[i].set_xlim(0, max(10, t.iloc[-1]))
    return lines.values()

ani = animation.FuncAnimation(fig, update, frames=len(df), interval=1000, blit=False, repeat=False)
plt.tight_layout()
plt.show()

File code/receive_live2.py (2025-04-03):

import matplotlib.pyplot as plt
import matplotlib.animation as animation
import socket
from math import sqrt, atan2, degrees

# Set up UDP
HOST = '0.0.0.0'
PORT = 5005
sock = socket.socket(socket.AF_INET, socket.SOCK_DGRAM)
sock.bind((HOST, PORT))
sock.settimeout(2)

# Data storage
time_data = []
temperature_data = []
altitude_barometric_data = []
altitude_gps_data = []
vertical_velocity_data = []
total_acceleration_data = []
vertical_acceleration_data = []
pitch_data = []
roll_data = []
yaw_data = []
pitch_rate_data = []
roll_rate_data = []
yaw_rate_data = []
drift_data = []
latitude_data = []
longitude_data = []

# Calibration references
prev_altitude = None
initial_lat = None
initial_lon = None
initial_total_acc = None
initial_vert_acc = None
initial_roll = None

# Plot setup
fig, ax = plt.subplots(3, 3, figsize=(16, 12))
ax = ax.flatten()

titles = [
    "Temperature vs Time", "Altitude (Barometric & GPS) vs Time", "Vertical Velocity vs Time",
    "Total Acceleration vs Time", "Vertical Acceleration vs Time", "Orientation (Pitch, Roll, Yaw)",
    "Angular Rates (Pitch, Roll, Yaw)", "Rocket Drift vs Time", "GPS 2D Path"
]
ylims = [
    (0, 50), (0, 250), (-12.5, 60),
    (0, 90), (0, 90), (-180, 180),
    (-25, 40), (0, 500), None
]

for i in range(9):
    ax[i].set_title(titles[i])
    if ylims[i]: ax[i].set_ylim(*ylims[i])
    ax[i].grid(True)

# Line definitions
lines = {
    "temperature": ax[0].plot([], [], label="Temp (°C)", color='red')[0],
    "alt_baro": ax[1].plot([], [], label="Baro (m)", color='blue')[0],
    "alt_gps": ax[1].plot([], [], label="GPS (m)", color='red')[0],
    "vertical_velocity": ax[2].plot([], [], label="Vert Vel (m/s)", color='green')[0],
    "total_acc": ax[3].plot([], [], label="Total Acc (m/s²)", color='purple')[0],
    "vert_acc": ax[4].plot([], [], label="Vert Acc (m/s²)", color='orange')[0],
    "pitch": ax[5].plot([], [], label="Pitch (°)", color='blue')[0],
    "roll": ax[5].plot([], [], label="Roll (°)", color='red')[0],
    "yaw": ax[5].plot([], [], label="Yaw (°)", color='green')[0],
    "pitch_rate": ax[6].plot([], [], label="Pitch Rate (°/s)", color='blue')[0],
    "roll_rate": ax[6].plot([], [], label="Roll Rate (°/s)", color='red')[0],
    "yaw_rate": ax[6].plot([], [], label="Yaw Rate (°/s)", color='green')[0],
    "drift": ax[7].plot([], [], label="Drift (m)", color='brown')[0],
    "gps_path": ax[8].plot([], [], label="GPS Path")[0],
}

for a in ax: a.legend()

# Update function
def update_plot(frame):
    global prev_altitude, initial_lat, initial_lon
    global initial_total_acc, initial_vert_acc, initial_roll

    try:
        data, _ = sock.recvfrom(1024)
        fields = data.decode("utf-8").strip().split(",")

        if len(fields) >= 15:
            temperature = float(fields[1])
            altitude = float(fields[2])
            gps_alt = float(fields[3])
            ax_, ay_, az_ = float(fields[4]), float(fields[5]), float(fields[6])
            gx_, gy_, gz_ = float(fields[7]), float(fields[8]), float(fields[9])
            lat, lon = float(fields[13]), float(fields[14])

            # Time
            t = time_data[-1] + 1 if time_data else 0
            time_data.append(t)

            # Base telemetry
            temperature_data.append(temperature)
            altitude_barometric_data.append(altitude)
            altitude_gps_data.append(gps_alt)
            latitude_data.append(lat)
            longitude_data.append(lon)

            # Vertical Velocity
            if prev_altitude is not None:
                vertical_velocity_data.append(altitude - prev_altitude)
            else:
                vertical_velocity_data.append(0)
            prev_altitude = altitude

            # Total acceleration (calibrated)
            total_acc = sqrt(ax_**2 + ay_**2 + az_**2)
            if initial_total_acc is None:
                initial_total_acc = total_acc
            total_acceleration_data.append(total_acc - initial_total_acc)

            # Vertical acceleration
            if initial_vert_acc is None:
                initial_vert_acc = az_
            vertical_acceleration_data.append(az_ - initial_vert_acc)

            # Orientation
            pitch = degrees(atan2(ay_, sqrt(ax_**2 + az_**2)))
            roll = degrees(atan2(ax_, sqrt(ay_**2 + az_**2)))
            yaw = degrees(atan2(az_, sqrt(ax_**2 + ay_**2)))
            if initial_roll is None:
                initial_roll = roll
            roll -= initial_roll
            pitch_data.append(pitch)
            roll_data.append(roll)
            yaw_data.append(yaw)

            # Angular Rates
            pitch_rate_data.append(gx_)
            roll_rate_data.append(gy_)
            yaw_rate_data.append(gz_)

            # Rocket Drift
            if initial_lat is None:
                initial_lat = lat
                initial_lon = lon
            drift = sqrt((lat - initial_lat)**2 + (lon - initial_lon)**2) * 111139
            drift_data.append(drift)

            # Update plots
            lines["temperature"].set_data(time_data, temperature_data)
            lines["alt_baro"].set_data(time_data, altitude_barometric_data)
            lines["alt_gps"].set_data(time_data, altitude_gps_data)
            lines["vertical_velocity"].set_data(time_data, vertical_velocity_data)
            lines["total_acc"].set_data(time_data, total_acceleration_data)
            lines["vert_acc"].set_data(time_data, vertical_acceleration_data)
            lines["pitch"].set_data(time_data, pitch_data)
            lines["roll"].set_data(time_data, roll_data)
            lines["yaw"].set_data(time_data, yaw_data)
            lines["pitch_rate"].set_data(time_data, pitch_rate_data)
            lines["roll_rate"].set_data(time_data, roll_rate_data)
            lines["yaw_rate"].set_data(time_data, yaw_rate_data)
            lines["drift"].set_data(time_data, drift_data)
            lines["gps_path"].set_data(latitude_data, longitude_data)

            # X-axis limits
            for a in ax[:8]:
                a.set_xlim(max(0, t - 100), t + 10)

    except socket.timeout:
        print("No data received (timeout)")

ani = animation.FuncAnimation(fig, update_plot, interval=1000, blit=False)
plt.tight_layout()
plt.show()

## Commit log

2025-03-31 Create cad
2025-04-08 Rename tubes v5.stl to Hermes Engine Protection.stl
    [Hermes Engine Protection.stl]
2025-04-10 Rename BT Engine Mount.stl to Hemres BT Engine Mount.stl
    [Hemres BT Engine Mount.stl]
2025-05-04 Update and rename Fligth1.csv to Flight1.csv
    [Flight1.csv]
2025-05-12 Update and rename Flight 4.2 Real.csv to Flight4.csv
    [Flight4.csv]
2025-05-12 Update and rename Fin_Aligner_24mm_4_fin.stl to Hermes Fin Aligner.stl
    This fin aligner was used to align the fins better. I found it from this link: https://www.thingiverse.com/thing:695599
    [Hermes Fin Aligner.stl]
